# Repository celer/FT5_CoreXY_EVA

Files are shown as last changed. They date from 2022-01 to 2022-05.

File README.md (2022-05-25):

# Introduction 

This is a OpenSCAD based utility to generate a Folgertech FT5 to coreXY using the EVA 
carriage system used on the Ratrig printers, this is a work in progress. 

I'm using OpenSCAD for the design so it is fully parametric fully bed movement
can be simulated and pulley and belt sizes can be changed so belt paths can 
be simulated. This means that you can modify the openscad file based upon 
your available pulleys and belt and the correct design will be generated
for you. 

I've downloaded the STLs from the EVA project into this repo for ease of
use, see here: https://main.eva-3d.page

Nema17 model is from here: https://www.thingiverse.com/thing:67561
Endstop model is from here: https://www.thingiverse.com/thing:2405504/files

This is a work in progress and no STLs for printing have been created yet. 

## Goals

 * Gain the benefits of CoreXY, primarly improved print speed and print quality
 * Reuse as many peices as I can from my existing FT5
 * Share with the community so that others can extend the lives of their FT5s

## Top View
 * [Parallel A-H belt paths](https://drmrehorst.blogspot.com/2018/08/corexy-mechanism-layout-and-belt.html)

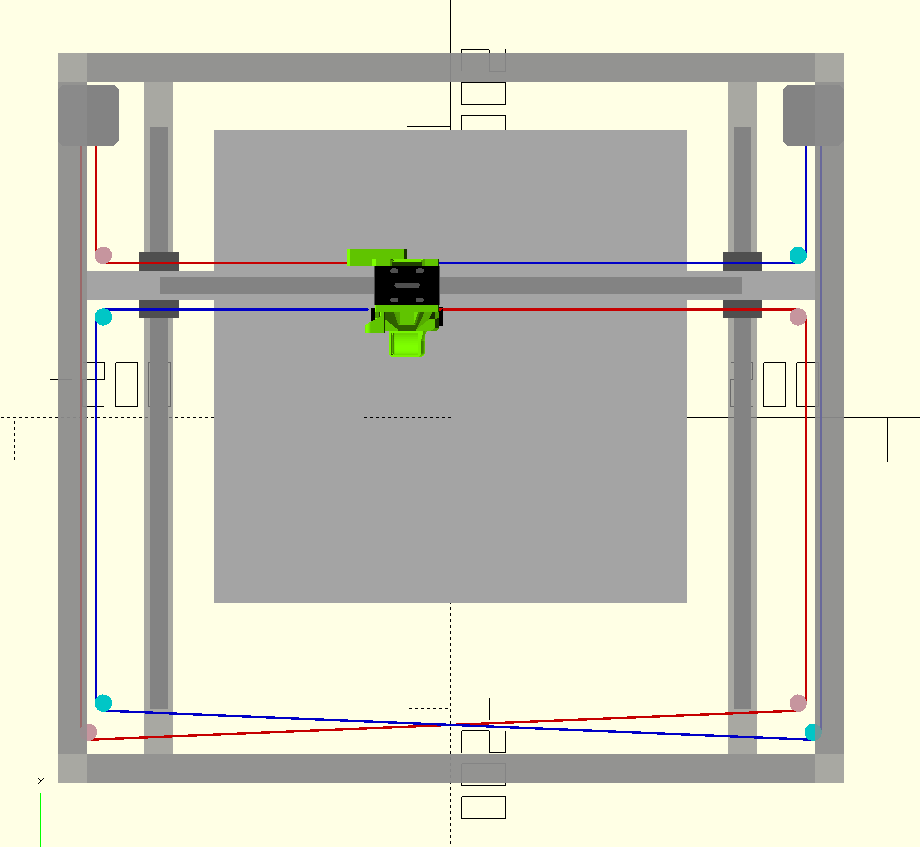
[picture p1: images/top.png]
Top


## Side views

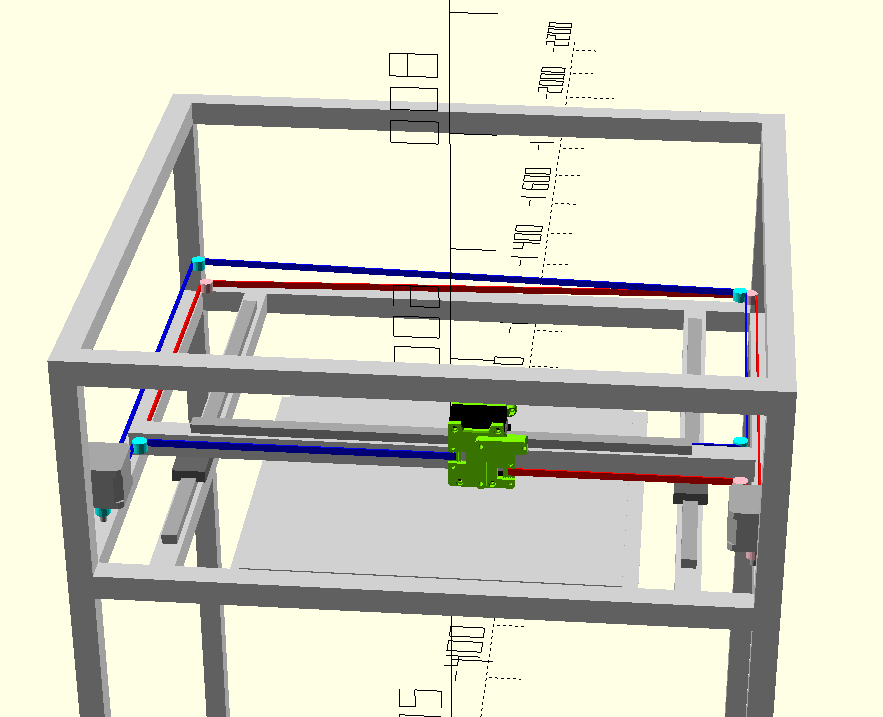
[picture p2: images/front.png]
Front

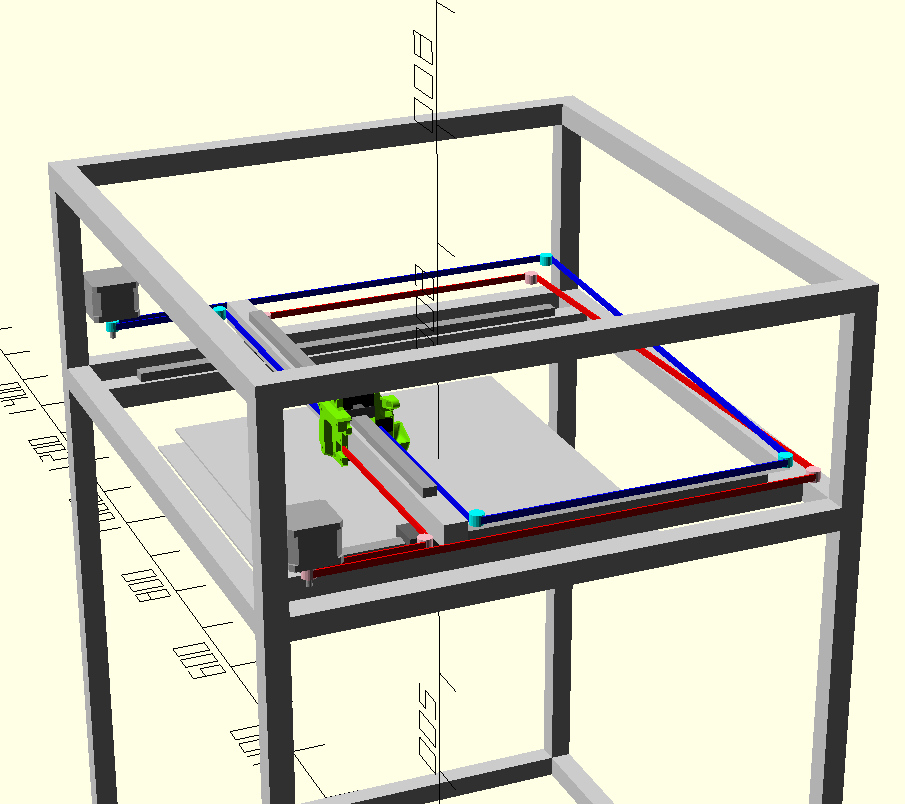
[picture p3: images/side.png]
Side

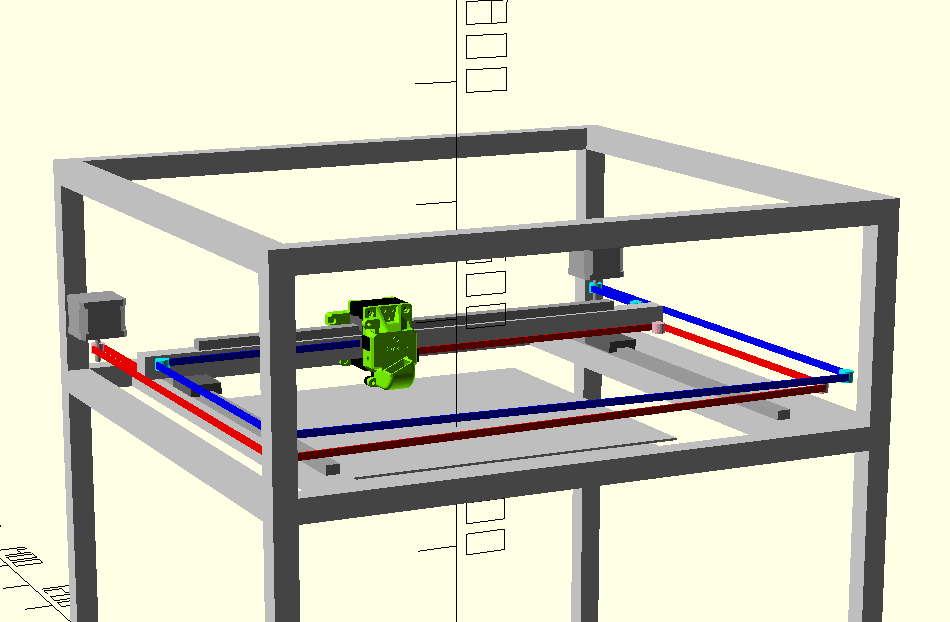
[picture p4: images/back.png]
Back


## Model view
Model

# Building

To build the stls you will need a linux environment with openscad installed, simply type 
'make' in the root of the directory and all the models will be generated. Or alternatively 
you can jump to the bottom of the .scad file and select specific models for printing. 

# Assembly

## Parts needed

See the bom.txt in this repo for a build of materials.

### Belts and Pulleys
The currently generated stls assume that you're using a Gates 6mm belt and pulleys, such 
a kit can be acquired from here: https://www.filastruder.com/products/gates-motion-set-for-railcore?_pos=5&_sid=bafef878a&_ss=r

I choose this belt kit because chinese / lesser quality belts stretch and may give poor results. 

This particular kit includes 2 smooth idler pulleys, 6 toothed idler pulleys, and 2 16 tooth motor pulleys. 

### Nuts and bolts

 * 20 M5x10MM bolts and t-slot nuts, which should be scavangable from your existing FT5 build
 * 2 M5x75MM bolts for the EVA carriage
 * An assortment of M3 
 * Shoulder bolts and shims for the pulleys - https://www.amazon.com/gp/product/B077GXK4P5/ref=ppx_yo_dt_b_asin_title_o08_s00?ie=UTF8&psc=1  https://www.filastruder.com/products/shims-for-shoulder-screws?_pos=1&_sid=fd8270e49&_ss=r

 ## What to print

  - You will need to print all the models in "stls/" folder, print these models with atleast 3 layer thickness, top bottom and side, and 40% infill.
  - You will need to choose and print an EVA extruder carriage, make sure to print the rear carriage tensors which allow for the teeth of the belts to face the rear of the printer
  - For the x axis you can either use your exisiting aluminum extrusion or go down the path of the carbon fiber square tube. I've included parts for the extrusion which are marked have the suffix *_al_2020.stl or *_cf_tube.stl which are for the carbon fiber square tube. See the section below on the carbon fiber square tube

## Assembly 

### Carbon Fiber Square Tube (optional)

Print out 2 copies of the xy_carriage_mount_cf_tube_upper_drill_jig.stl and use these two parts to align the holes to drill on the carbon fiber tube, the drill jig is setup so that it aligns the holes for the linear rail and then mounting brackets. I have not tested this drill jig, so you should use it with caution. You essentially drill the holes to mount the linear rail and end mounts, drilling through both sides of the square tube, find them smallest 1/4" socket which fits the M3 nuts required to attach the linear rail to the square tube and enlarge the holes on the bottom of the square tube so that you can fight the socket into the holds to tighten the linear rail to the carbon fiber rod. 
 
### Assemble the X rail 

1. Remove the old FT5 components 
2. You will need to insure that the XY carriage uppers and lowers have the 'F' near the front of the printer, the carriages are not symmetric front to back. 

### Assemble the Y rail

1. Remove the old FT5 components
2. Remove the top aluminum extrusion rail and assemble the motor mounts and rear pulley mounts with appropriate M5 and tslot nuts then with the top rectangle of the aluminum extrusion removed from the printer slide the motor and rear pulley mounts down into place. 

### Attach the belts

1. When attaching the belts you'll need to insure that the belts are level and parrallel to the main axis of the printer. 
2. Add the Y endstop

# Included Marlin settings

I have included my marlin Configuration.h and Configuration_adv.h

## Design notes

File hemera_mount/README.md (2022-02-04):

# Introduction

This is my quick and dirty corexy hemera mount which uses the same belt mounting locations as the EVA carriages. 

 * Compatible cable mounts to EVA mounting system
 * BL Touch mount
 * Cable mount

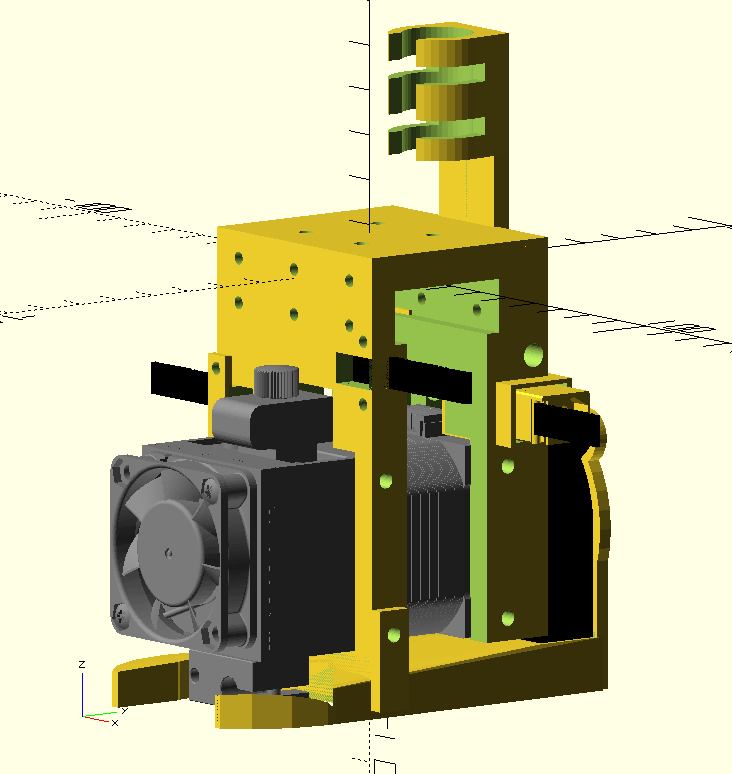
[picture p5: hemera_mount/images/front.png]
Front


# Notes
 
 * The "rear_eva_9mm_tension_slider.stl" is exported from the EVA repo (https://main.eva-3d.page/)
 * The Hemera model comes from https://www.thingiverse.com/thing:4016291/files by e3dsupport
 * The blower fan comes from https://www.thingiverse.com/thing:1576438/files by jimustanguitar

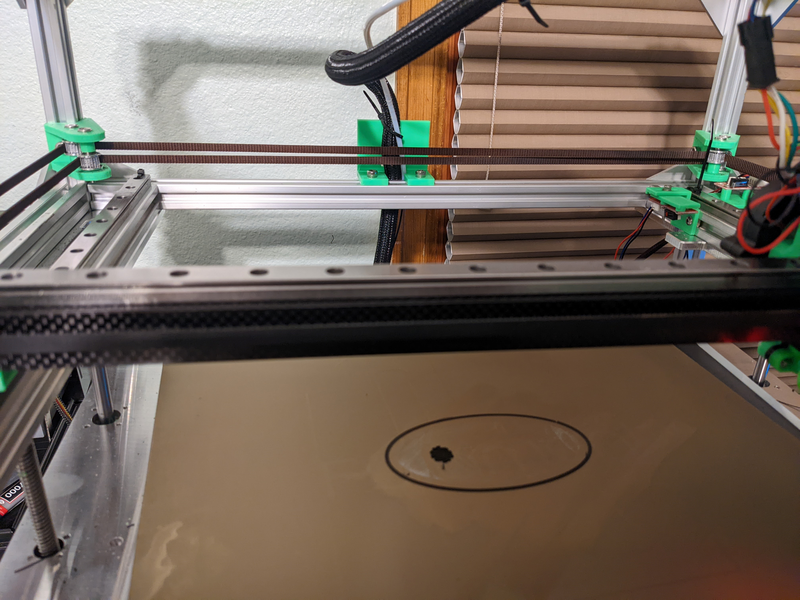
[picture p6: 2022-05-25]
photos/PXL_20220525_043905156.jpg.png

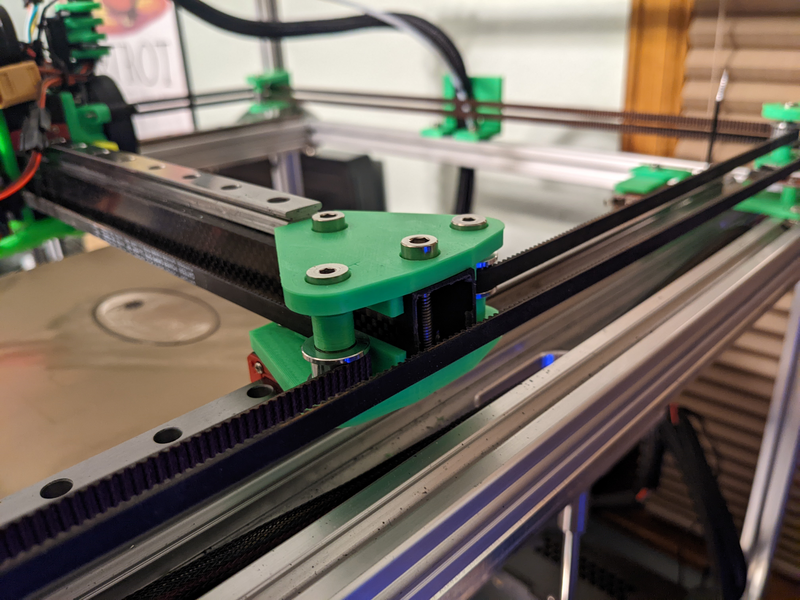
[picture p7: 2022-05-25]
photos/PXL_20220525_043838924.MP.jpg.png

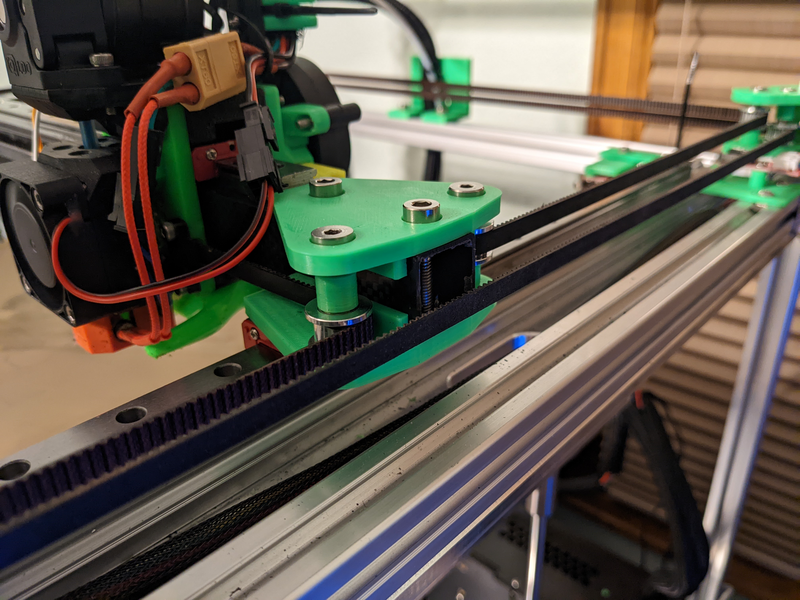
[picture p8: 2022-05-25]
photos/PXL_20220525_043833367.MP.jpg.png

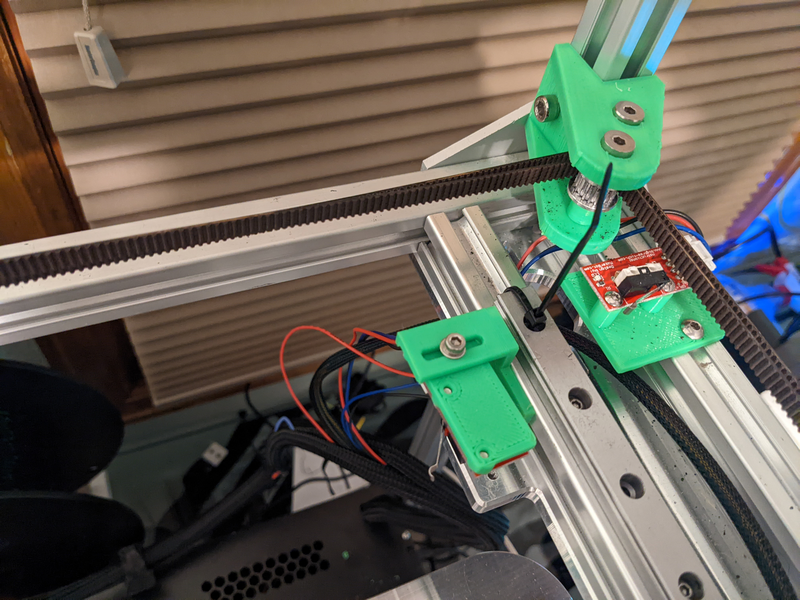
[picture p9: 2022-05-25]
photos/PXL_20220525_043824527.jpg.png

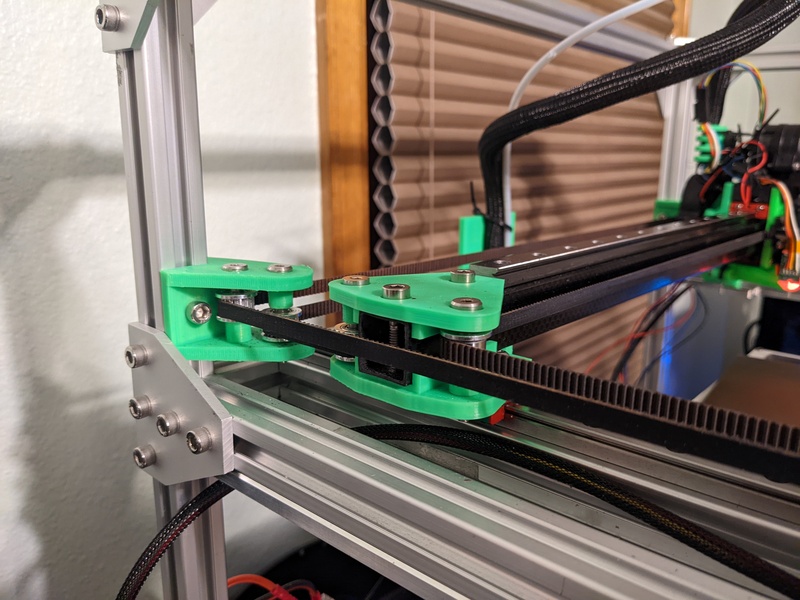
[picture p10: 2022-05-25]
photos/PXL_20220525_043754034.jpg.png

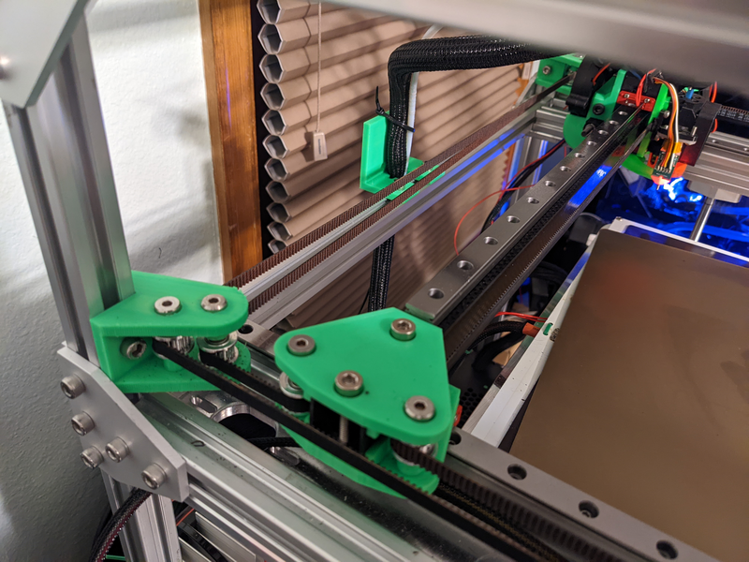
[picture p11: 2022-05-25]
photos/PXL_20220525_043800626.jpg.png

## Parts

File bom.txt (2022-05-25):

Raspberry PI 3b+

See this list for what is compatible with klipper

https://www.klipper3d.org/FAQ.html#can-i-run-klipper-on-something-other-than-a-raspberry-pi-3

From Ali Express (Carbon Fiber Square Tube for X Axis, optional):

1 X 20x20x500mm (the 500m is the only length they offer) 

https://www.aliexpress.com/item/32946654825.html?spm=a2g0o.order_list.0.0.dd8b1802j7lyNM

From BIQU: 

BIQU Phaetus Dragon Hotend (Make sure to select High Flow Option) (Optional)

https://www.biqu.equipment/products/bigtreetech-dargon-hotend-all-metal-copper-alloy-0-4mm-extruder-head-for-3d-printer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

F446 Controller Board (Make sure to select with 8 TMC2209 drivers), this is way overkill but it’s what is currently available. (Optional)

https://www.biqu.equipment/collections/control-board/products/bigtreetech-octopus-pro-v1-0-chip-f446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

From Printed Solid

Drive motor (There are two other alternatives to this the LGX Mini or the Sherpa Mini, I haven’t tested the options well enough to have a solid opinion on which one is the best - this is the one I’m currently testing, I think it’s better than the Sherpa mini, and will test an LGX mini soon):

https://www.printedsolid.com/products/bondtech-lgx-lite-large-gears-extruder?variant=39664965877845
 
or

https://www.printedsolid.com/products/ldo-orbiter-v2-dual-drive-direct-extruder

BL Touch (These are used to profile the bed level)
https://www.printedsolid.com/products/bltouch-automatic-bed-leveling-probe

From Filstruder:

Shims for pulleys

https://www.filastruder.com/products/shims-for-shoulder-screws?_pos=1&_sid=fd8270e49&_ss=r

Gates Belt Kit for RailCore Printer 300 ZL 

https://www.filastruder.com/products/gates-motion-set-for-railcore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

2 X Drive motors (42STH48-2504AC) - Optional, these enable higher speed printing, I haven’t fine tuned mine yet, but they should work better than the folgertech stepper motors

https://www.filastruder.com/products/ldo-stepper-motors-all-types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

From Amazon:

High performance bowden tube to keep the filament from spooling backwards

https://www.amazon.com/dp/B07PS3NH82?psc=1&ref=ppx_yo2ov_dt_b_product_details

These take the play out of the Z Axis (Optional)

https://www.amazon.com/gp/product/B08TLVL95C/ref=ppx_yo_dt_b_asin_title_o01_s00?ie=UTF8&psc=1

Anti-Vibration Feet, stop the rocking the printer does at high speed

https://www.amazon.com/dp/B0711Y6T56?psc=1&ref=ppx_yo2ov_dt_b_product_details

2 X Larger Z axis pulleys, these allow you to 2x the X axis resolution, you’ll also need a new belt, but I don’t know what size you’d need to measure after you test fit these: 

https://www.amazon.com/gp/product/B07K6BRL4K/ref=ppx_yo_dt_b_asin_title_o04_s00?ie=UTF8&psc=1

For the carbon fiber tube (Optional if you want to run carbon fiber x axis)

https://www.amazon.com/dp/B073TRJP6K?psc=1&ref=ppx_yo2ov_dt_b_product_details

1 set of M3 nuts (Optional if you want to run a carbon fiber x axis)
https://www.amazon.com/dp/B071NLDW56?psc=1&ref=ppx_yo2ov_dt_b_product_details

1 set of M3 washers (Optional if you want to run carbon fiber x axis)
https://www.amazon.com/dp/B075GVHLQ4?psc=1&ref=ppx_yo2ov_dt_b_product_details

You may need these for the hot end
https://www.amazon.com/dp/B08R9G2VDR?ref=ppx_yo2ov_dt_b_product_details&th=1

Shoulder Bolts, these are used on the corner pulleys and x axis
https://www.amazon.com/gp/product/B077GXK4P5/ref=ppx_yo_dt_b_asin_title_o08_s00?ie=UTF8&psc=1

HDMI Touchscreens & cables to hook up to the Raspberry PIs - You can choose any raspberry pi touch screen, the one I linked is the one I have, you’ll need cables as well. 
https://www.amazon.com/gp/product/B09LLC4H3Q/ref=ppx_yo_dt_b_search_asin_title?ie=UTF8&th=1

Set of fans 40x40x10 for the hot ends::
https://www.amazon.com/gp/product/B088BF6H8P/ref=ppx_yo_dt_b_asin_title_o00_s00?ie=UTF8&psc=1

Misc hardware:

8x M5x30 metric bolts & nuts 
4x M5x75 metric bolts & nuts

You’ll probably need extra wires, and some misc metric hardware.

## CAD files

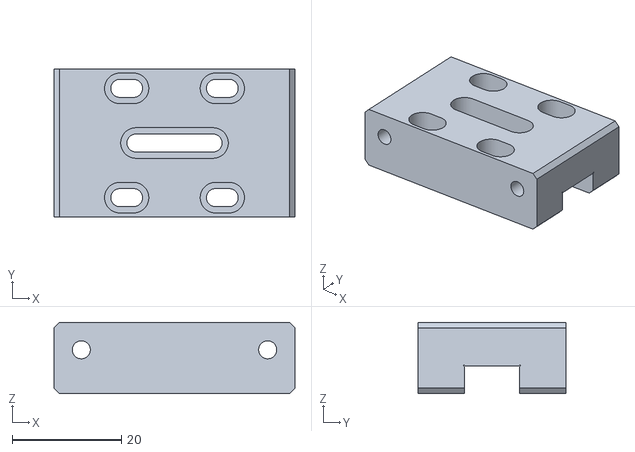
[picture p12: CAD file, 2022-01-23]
eva_hemera/top_mgn12.stl
44.1 x 27.0 x 13.0

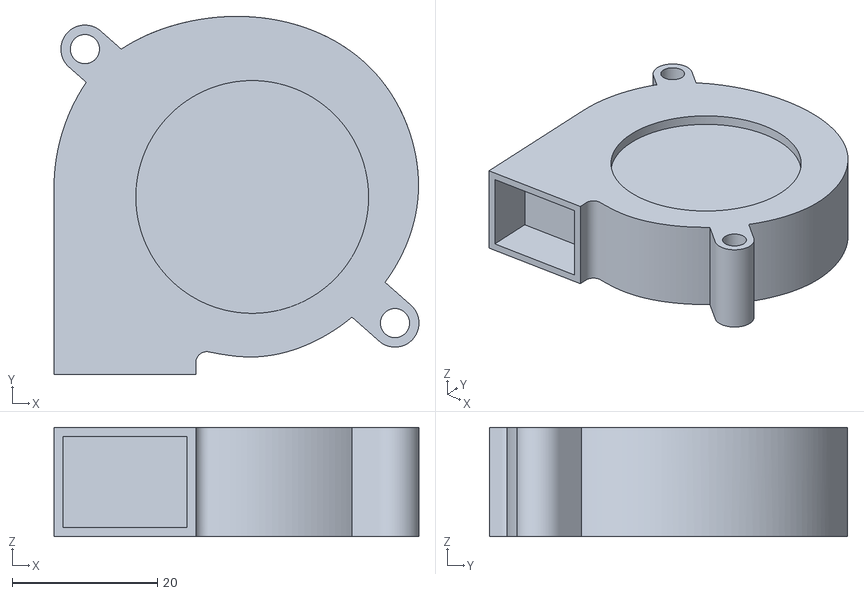
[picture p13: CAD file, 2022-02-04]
hemera_mount/models/5015_Blower_Fan.stl
50.2 x 49.2 x 15.0

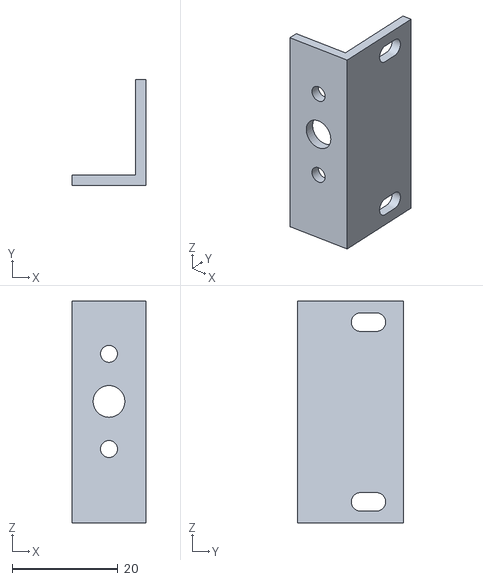
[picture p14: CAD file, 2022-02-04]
hemera_mount/stls/bl_touch_mount.stl
14.0 x 20.0 x 42.0

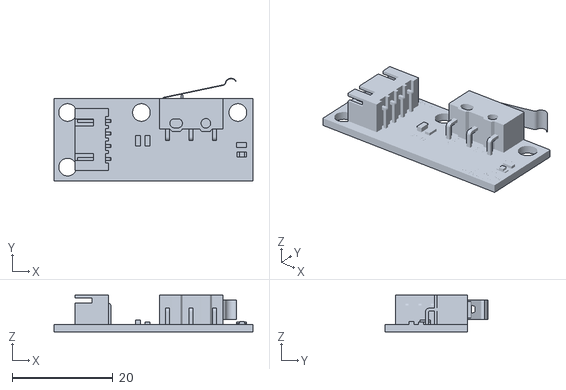
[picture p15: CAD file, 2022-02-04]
models/MakerBot_Endstop.stl
39.5 x 20.3 x 7.30

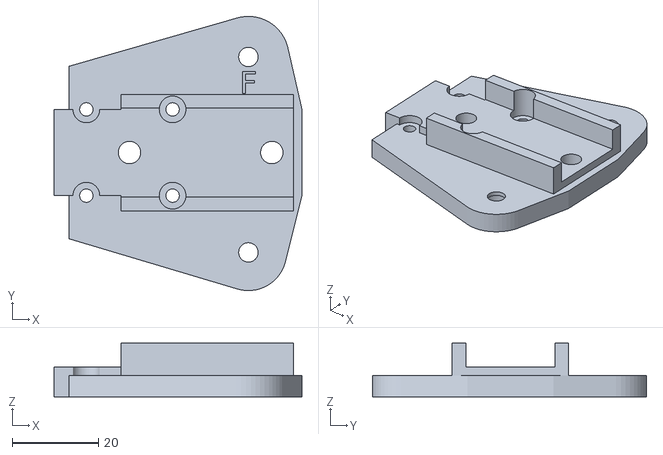
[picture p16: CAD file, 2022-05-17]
stls/left_xy_carriage_mount_lower_cf_tube.stl
57.5 x 63.6 x 12.5

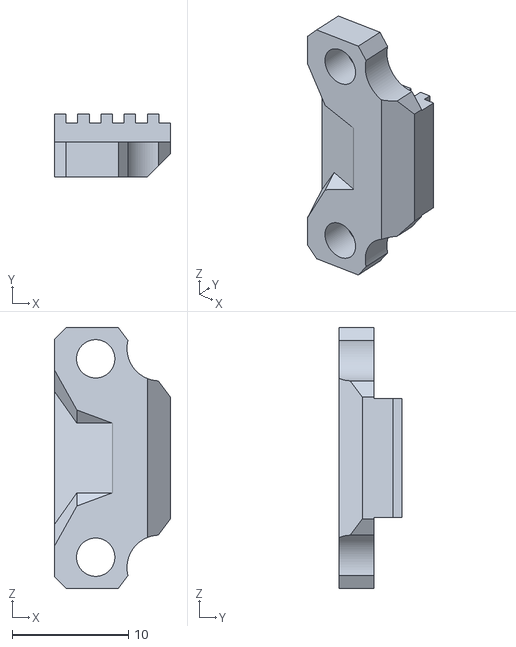
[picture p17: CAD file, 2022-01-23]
eva_hemera/face_belt_grabber.stl
10.0 x 5.40 x 22.5

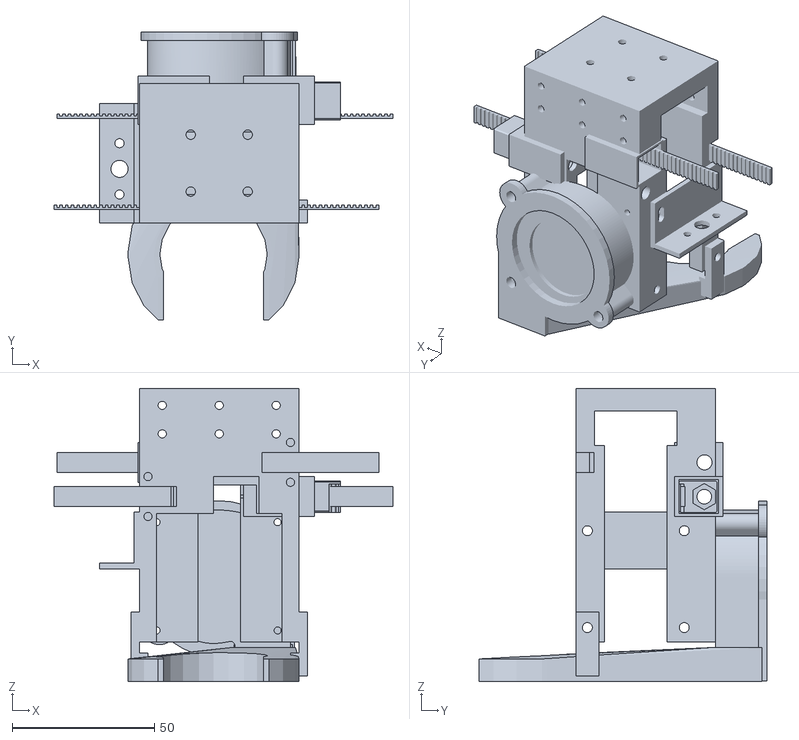
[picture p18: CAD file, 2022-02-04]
hemera_mount/stls/hemera_eva.stl
119.0 x 101.0 x 103.0

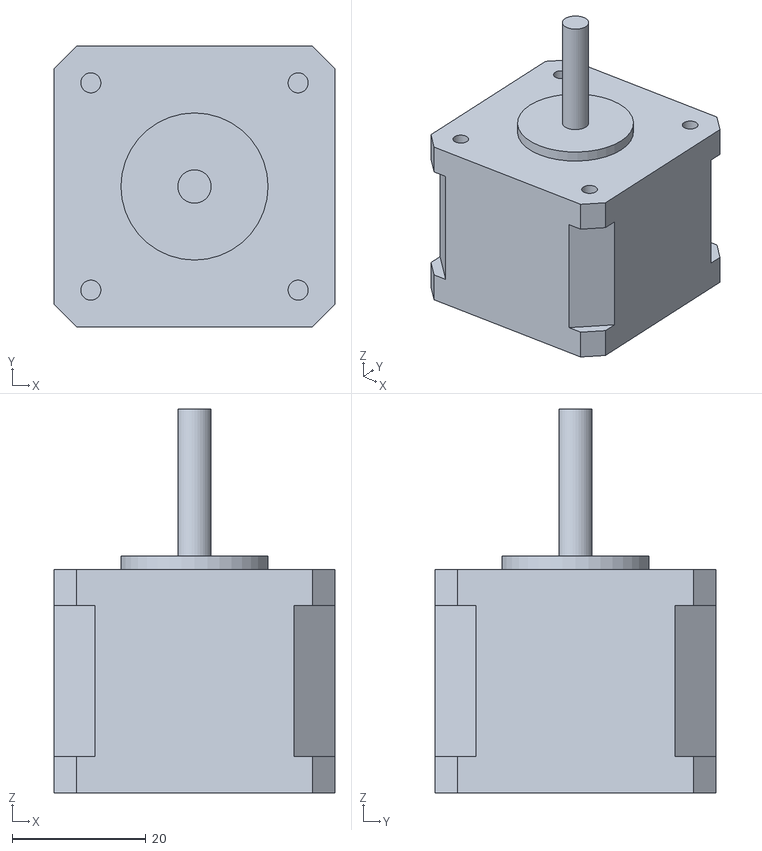
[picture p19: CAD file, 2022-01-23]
models/Motor_NEMA17.stl
42.0 x 42.0 x 57.4

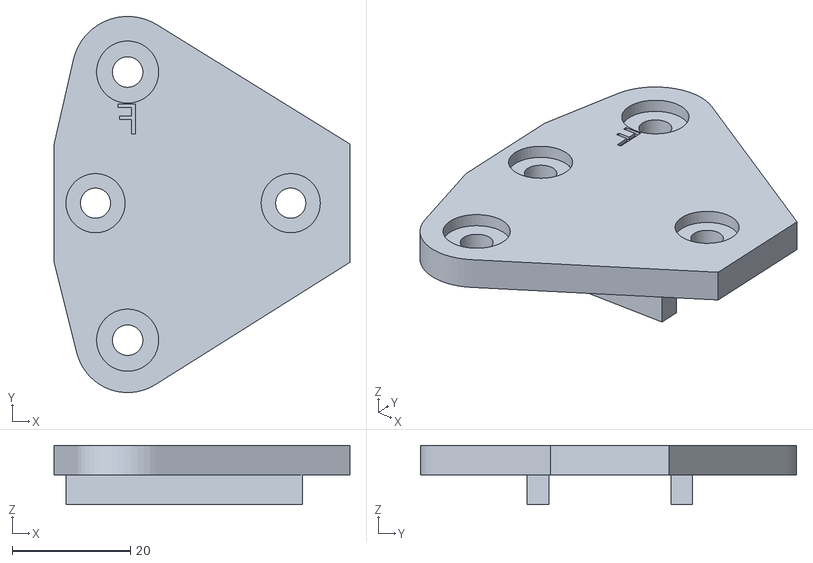
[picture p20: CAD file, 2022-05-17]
stls/right_xy_carriage_mount_upper_cf_tube.stl
50.0 x 63.6 x 10.0

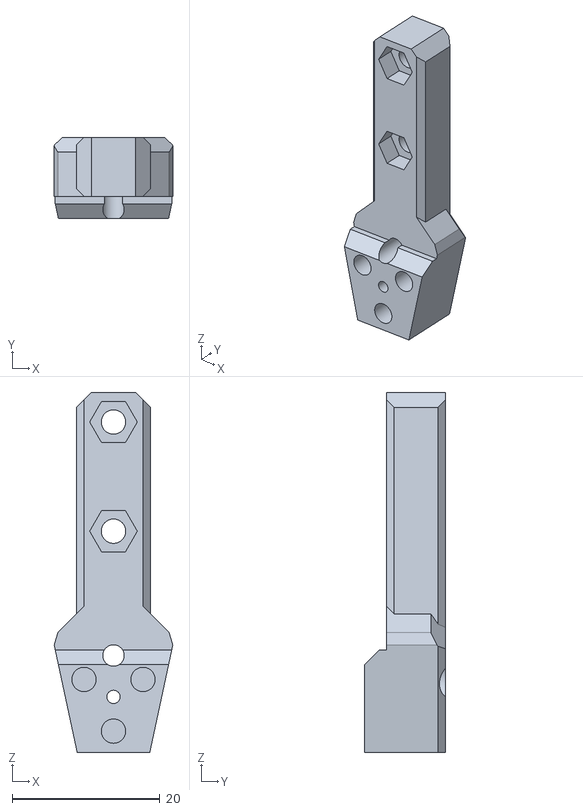
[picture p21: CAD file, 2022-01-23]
eva_hemera/unversal_cable_mount.stl
16.1 x 11.0 x 48.8

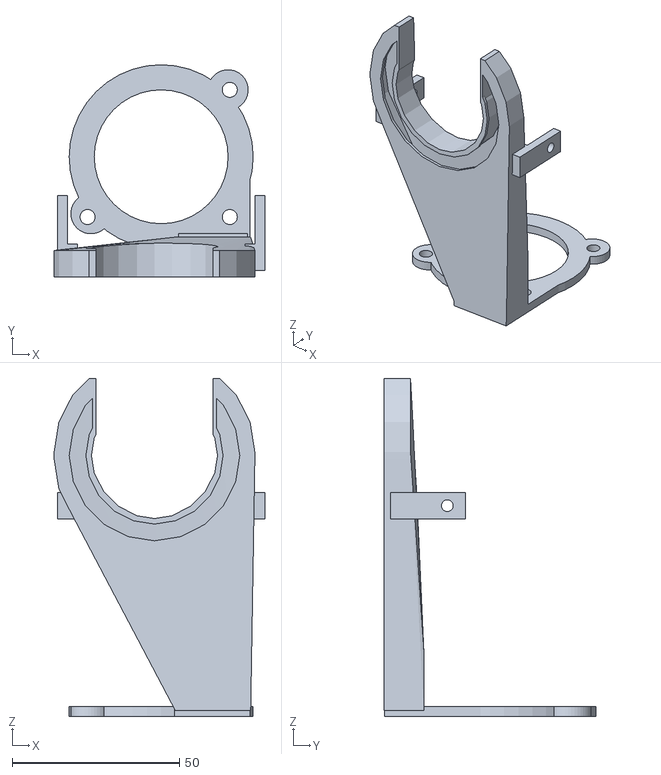
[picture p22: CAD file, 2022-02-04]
hemera_mount/stls/duct.stl
63.0 x 63.5 x 101.0

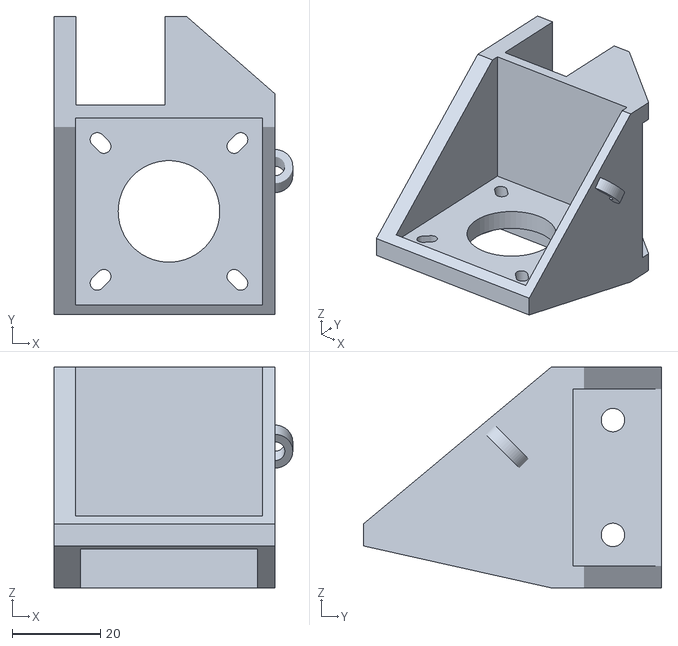
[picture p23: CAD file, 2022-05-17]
stls/right_motor_mount.stl
54.1 x 67.5 x 50.0

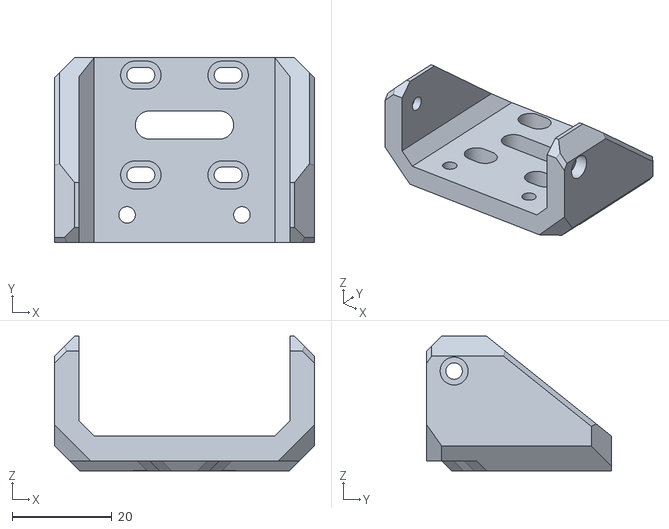
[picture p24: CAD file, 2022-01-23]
eva_hemera/top_lgx_mgn12_b.stl
52.1 x 37.0 x 27.0

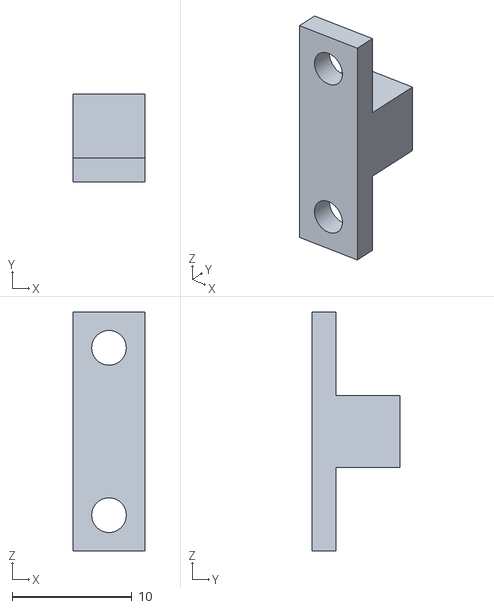
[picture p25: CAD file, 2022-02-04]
hemera_mount/stls/front_belt_mount.stl
6.00 x 7.32 x 20.0

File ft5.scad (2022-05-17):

// Introduction    //////////////////////////////////////////////
/////////////////////////////////////////////////////////////////
// 1. Measure and define your pulleys
//
// To get a CoreXY system working well the belts *MUST* be parallel
// to the axies, which means we need to accurately measure our belts
// and pulleys.
// 

// 1. Pulley definitions ///////////////////////////////////////////
////////////////////////////////////////////////////////////////////
// The pulley definitions define details about the pulleys which are critical to getting
// a precise corexy movement, the front belts MUST be parallel to their respective axis.

// The DWB = Diameter with belt - this the measurement of the diameter of the pulley
// with the belt on it. 

//// Motor pully definitions

///// Motor Pulley Height
MotorPulleyH = 16;   

//// Motor Pulley Diamater With Belt
MotorPulleyDWB = 11.04;

//// X Axis Pulleys
////////////////////////////////////////////////////////////////////
// X Axis Pulley details, I have accounted for the smooth pullyes seperately because
// they will have a different diameter than the toothed pulleys

// X Pulley Smooth Height
XPulleySmoothH = 10;
// X Pulley Smooth Diameter with Belt
XPulleySmoothDWB = 14.82;

// X Axis Pulley details, this can be toothed or smooth
// X Pulley Toothed Height
XPulleyToothedH = 10;
// X Pulley Toothed Diameter with Belt
XPulleyToothedDWB = 13.72;

// Rear left and right corner Pulley details
CornerPH = 10; // Height
CornerPDWN = 13.72; // Outside diameter with belt
CornerPulleyMountSpacer=1;

//////////////////// FT5 Dimensions //////////////////////////////////////////////
//
// I've measured these somewhat accurately but thit's worth double checking.
//
// This is the distance between the centers of the exterior 2020 extrusions, measured 
// at center
ExteriorWidth = 520;
ExteriorDepth = 482;

// The inteior space of the XY carriage area 
// measured center of extrusion to center of extrusion
InteriorWidth = ExteriorWidth-100;

InteriorDepth = ExteriorDepth;

// Center of XY Carriage height
XYCarriageHeight = 532;

// Total Length of the 2020 extrusion for the X axis
X2020Length = ExteriorWidth-20;

// FIXME this has an issue with hitting the Y blocks. 
// How far off the Y MGN12 block the X 2020 extrusion is
XCarriageMountHeight = 7;

// Overall height of the printer
Height = 720;

//This is how thick the belt is so the front pulleys can be placed correctly
BeltThickness = 1.50;

// The height of the belt, in theory changing this to a wider belt should just work
BeltHeight = 5.8;

MotorX = 42.3;
MotorY = 42.3;

// Total height of an MGN12 rail and block 
MGN12Height = 13;

//How much to offset each pulley so that doesn't interfer with the others
RearPulleyOffset = 10;


// Z Axis dimensions
ZAxisLinearRodOffsetsFromFront=[117,317];
ZAxisMotorOffset=215.5;
ZAxisSideOffset=60;

// Enclosure
EnclosureWidth=495;
EnclosureHeight=172;
EnclosureDepth=78+5;

///////////////////////////////////////////// EVA Platform ////////////////////////////////
/// The EVA Carriage platform is meant to allow easy swapping of carriages so this is used
// by the ratrig guys to make it easy to support multiple extruders. 
// see https://main.eva-3d.page/

// Belt Offsets as calculated from the center of X MGN12 block
EVAFrontBeltY = 15.5;

// Center of the belt offset as calculated from the center top of the MGN12 block
EVAFrontUpperBeltZ = -18;
EVAFrontLowerBeltZ = -30;

// Center of the belt offset as calculated from the center top of the MGN12 block
EVAFrontUpperBeltX = 17;
EVAFrontLowerBeltX = -26;

// Belt Offsets as calculated from the X block
EVABackBeltY = -16.5;

EVABackLowerBeltZ = -30;
EVABackUpperBeltZ = -18;

EVABackLowerBeltX = 20;
EVABackUpperBeltX = -27;

Extrusion2020Height = 20;
Extrusion2020Width = 20;

/*
EVABackLowerBelt() color("red") cube([20,1.6,6],center=true);
EVABackUpperBelt() color("blue") cube([20,1.6,6],center=true);

EVAHemeraCarriage();*/

///////////////////////////////////////// BED Details /////////////////////////////////////////

// The bed is 35mm forward of the Y center, AFAIK
BedCenterY = 35;

BedX = ExteriorWidth-220+25;
BedY = 325;

////////////////////////////////////////// XY Carriage center on the bed /////////////////////////
// Change this to simulate movement
X = 150;  //(-150 to 150)
Y = 150;  //(-150 to 150)


// Calculated location
YLocation = InteriorDepth/2 - BedCenterY+X;
XLocation = InteriorWidth/2 + Y;


// Calculated upper and lower belt heights
LowerBeltHeight = XYCarriageHeight + Extrusion2020Height/2 +
                MGN12Height + XCarriageMountHeight + Extrusion2020Height + MGN12Height + EVAFrontLowerBeltZ;

UpperBeltHeight = XYCarriageHeight + Extrusion2020Height/2 + 
                MGN12Height + XCarriageMountHeight + Extrusion2020Height + MGN12Height + EVAFrontUpperBeltZ;

//cube([520,20,20],center=true);
//translate([0,0,XYCarriageHeight-10]) cube([400,20,20],center=true);



module frame(){
     union() color("lightgrey") {
        for(x=[-ExteriorWidth/2,ExteriorWidth/2]){
            for(y=[-ExteriorDepth/2,ExteriorDepth/2]){
                  translate([x,y,Height/2]) cube([20,20,Height],center=true); 
            }
        }
                
   
        // XYCarriage
        translate([0,-ExteriorDepth/2,XYCarriageHeight]) cube([ExteriorWidth-20,20,20],center=true);
        translate([0,ExteriorDepth/2,XYCarriageHeight]) cube([ExteriorWidth-20,20,20],center=true);
        
        translate([-ExteriorWidth/2,0,XYCarriageHeight]) cube([20,ExteriorDepth-20,20],center=true);
        translate([ExteriorWidth/2,0,XYCarriageHeight]) cube([20,ExteriorDepth-20,20],center=true);
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

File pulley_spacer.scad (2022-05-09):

$fn=40;


translate([0,12,0]) difference(){
    cylinder(r=10/2,h=10);
    cylinder(r=5.15/2,h=12);
}

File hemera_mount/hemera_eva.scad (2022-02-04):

/*
    Sorry this is quite a bit of a mess, and is carried over from a prior design
*/

// Belt Offsets as calculated from the center of X MGN12 block
EVAFrontBeltY = 15.5;

// Center of the belt offset as calculated from the center top of the MGN12 block
EVAFrontUpperBeltZ = -18;
EVAFrontLowerBeltZ = -30;

// Center of the belt offset as calculated from the center top of the MGN12 block
EVAFrontUpperBeltX = 17;
EVAFrontLowerBeltX = -26;

// Belt Offsets as calculated from the X block
EVABackBeltY = -16.5;

EVABackLowerBeltZ = -30;
EVABackUpperBeltZ = -18;

EVABackLowerBeltX = 20;
EVABackUpperBeltX = -27;

module stepper_mount_holes(){
	translate([0,-38,-17]){
		for(x=[0,34]){
			for (y=[0,34]){
				translate([0,y,x]) rotate([0,90,0]) cylinder(r=3.5/2,h=100,center=true);
			}
		}
	}
}


module mount() {
    difference(){
        union(){
            translate([0,0,-38]) rotate([90,0,0]) difference(){
                
                //Main block
                union(){
                    translate([0,1.5,-3.5]) cube([56,86+3,42+7],center=true);
                
                    
                    translate([0,1.5,-42/2]) difference(){
                        cube([56,86,7],center=true);
                    }
                    

                }
                
                fan_holes(2.5);
                
                // Screw holes for mounts
                for(x=[-20:20:20]){
                    for(y=[-5,5]){
                        translate([x,35+y,25]) cylinder(r=2.9/2,h=90,center=true);
                        translate([x,35+y,-25]) cylinder(r=2.9/2,h=90,center=true);
                    }
                }
                
                // Cut out for the rail and slider
                translate([0,32,0]) cube([100,12,29],center=true);
                translate([0,-6,0]) cube([100,88,22],center=true);


                // Cut out for the stepper motor
                translate([0,-23,0]) cube([44,50,43],center=true);
                
                // Cut out for rear stepper cables
                translate([0,-20,-12]) cube([26,64,19],center=true);
                
                // Cut out for rear stepper cables
                translate([0,-20,-22]) cube([15,64,19],center=true);
                
                // Cut out for front handle
                translate([6,-20,20]) cube([16,70,50],center=true);
                
                
                // Mounts for the stepper motor
                stepper_mount_holes();
                

                
                //Slide rail mounts
                for(x=[-10,10]){
                    for(z=[-10,10]){
                        translate([x,40,z]) rotate([90,0,0]) cylinder(r=3.3/2,h=20,center=true);
                    }
                }     
            }
           
 
           
            translate([EVABackUpperBeltX,-EVABackBeltY,EVABackUpperBeltZ]) translate([11,5.6,0]){
                cube([25,17,14],center=true); 
            }
            translate([EVABackLowerBeltX,-EVABackBeltY,EVABackLowerBeltZ]) translate([1,5.6,0]) {
                cube([25,17,14],center=true);
            }
        }
        
        translate([EVABackUpperBeltX,-EVABackBeltY,EVABackUpperBeltZ]) translate([10,5.6,0]){
            cube([25,14,12],center=true); 
            translate([0,2,0]) rotate([0,90,0]) cylinder(r=5.3/2,h=200,center=true);
        }
        translate([EVABackLowerBeltX,-EVABackBeltY,EVABackLowerBeltZ]) translate([2,5.6,0]) {
            cube([25,14,12],center=true);
            translate([0,2,0]) rotate([0,90,0]) cylinder(r=5.3/2,h=200,center=true);
        }
        for(y=[0:-0.6:-10]){
            translate([EVAFrontLowerBeltX-2,-EVAFrontBeltY+y,EVAFrontLowerBeltZ]) gt2_belt(); 
            translate([EVAFrontUpperBeltX-2,-EVAFrontBeltY+y,EVAFrontUpperBeltZ]) gt2_belt();
        } 
      
        translate([EVAFrontLowerBeltX+1,-EVAFrontBeltY,EVAFrontLowerBeltZ]) rotate([90,0,0]) {
            for(z=[-7,7]){
                translate([0,z,5]) cylinder(r=2.9/2,h=10,center=true);
            }
        }
        translate([EVAFrontUpperBeltX+8,-EVAFrontBeltY,EVAFrontUpperBeltZ]) rotate([90,0,0]) {
            
            for(z=[-7,7]){
                translate([0,z,5]) cylinder(r=2.9/2,h=10,center=true);
            }
        }
        
        rotate([90,0,0]) translate([0,-38,0]) fan();
    }
    

   
}

//front_belt_mount();
cable_mount();
//mount();

module cable_mount(){
    translate([0,29,9]){
        difference(){
            union(){
                hull(){
                    translate([0,-10,15]) cylinder(r=22/2,h=27);
                    translate([0,0,28.5]) cube([20,4,27],center=true);
                }
                translate([0,0,11]) cube([20,4,62],center=true);
            }
            //translate([0,-13,25]) cylinder(r=16/2,h=50,center=true);
            translate([0,-10,25]) cylinder(r=16/2,h=50,center=true);

            for(z=[0:12:25]){
                translate([0,-17,22+z]) cube([24,24,4],center=true);
            }
            
            translate([0,-17,29]) cube([10,10,40],center=true);

            


        translate([0,0,-12]){
        for(z=[5,-5]){
            translate([0,0,z]) rotate([90,0,0]) cylinder(r=3.3/2,h=560,center=true);
        }   
    }
    }
    }
}

front_belt_mount();

module front_belt_mount(){
        
     
        difference(){
            union(){
                translate([EVAFrontLowerBeltX-2 ,-EVAFrontBeltY-3,EVAFrontLowerBeltZ]) translate([0,-3.4,-3])  cube([6,6,6]);
                translate([EVAFrontLowerBeltX-2 ,-EVAFrontBeltY-3,EVAFrontLowerBeltZ]) translate([0,-4.9,-10])  cube([6,2,20]);
            }
            for(z=[-7,7]){
                translate([EVAFrontLowerBeltX+1,-EVAFrontBeltY-3,EVAFrontLowerBeltZ+z]) rotate([90,0,0]) cylinder(r=2.9/2,h=1000,center=true);
            }
            translate([EVAFrontLowerBeltX-2,-EVAFrontBeltY+0.2,EVAFrontLowerBeltZ]) gt2_belt(); 
       }

        
        
}

module gt2_belt(len=12){
    translate([0,-1.55/2,-3.5]){
        cube([len,1.55-0.75,7]);
        for(r=[0:2:len]){
            translate([r,0,0]) cube([1.0,1.55,7]);
        }   
    }
}

module bl_touch_mount(){
	difference(){
		translate([-30,-17.8+0.4,-42/2]){
			cube([2,20,42]);
			translate([-12,0,0]) cube([12,2,42]);
		}
		bl_touch();
		for (z=[-1.5:0.25:1.5]){
			translate([0,z,0]) stepper_mount_holes();
		}
	}
}

module bl_touch(){
	translate([-35,-17.8+0.4,2]){ 
		rotate([90,0,0]) cylinder(r=8/2,36.3);
		rotate([90,0,0]) translate([0,0,-10]) cylinder(r=6/2,h=10);
		for(z=[9,-9]){
			translate([0,0,z]) rotate([90,0,0])translate([0,0,-10]) cylinder(r=3.2/2,h=10);
		}
	}
	
}

module hemera(){
	   translate([-24,-62.6,-20.5]) import("models/HEMERA-MODEL-1.1.STL");

}


module airflow_exitfan(d=0){
     translate([5.25,-56,-40.25-3]) cube([20.5,10+d,15.5]);
}



nozzle_x=-2;
nozzle_y=-53;
nozzle_z=32;

module airflow_exhaust(d=0,r=58,h=6){
    // translate([-20,-71+d,25]) rotate([0,-30,0]) cube([8,5,20]);
	translate([nozzle_x,nozzle_y,nozzle_z]) rotate([90,0,0]) translate([0,0,d]){ 
			cylinder(r=r/2,h=h,center=true,$fn=20);
	}
}



module airflow(){
        difference(){
            hull(){
                airflow_exitfan(); 
                airflow_exhaust();
            }
			
			airflow_exhaust(r=40,h=100);
			translate([nozzle_x,nozzle_y,nozzle_z+25]) cube([37,20,60],center=true);
					
        }   
}

module airflow_fins(){
	intersection(){
	intersection(){
		intersection(){
			union(){
				 for(x=[-24:6:26]){
					translate([x-2,-55,10]) cube([1.2,20,60],center=true);
				}
			}
			
			translate([0,0,10]) airflow();
			
		}
		translate([0,0,0]) airflow();
	}
	}
}


module duct(){
	
	//airflow_fins();
	
    difference(){
		union(){
		   
			translate([0,-21,-46])  difference(){
				union(){
					translate([4,-35.8,0]) cube([22.5,37,3]);
					cylinder(r=55/2,h=3);
					
					translate([20,20,0]) cylinder(r=12/2,h=3);
					translate([-21,-17,0]) cylinder(r=12/2,h=3);
					
					translate([0,-30,63]) difference(){
						cube([62,8,8],center=true);
						cube([50,8,8],center=true);

					}
					translate([0,-22,63]) difference(){
						cube([62,21,8],center=true);
						cube([56,21,8],center=true);
					}
				}
				cylinder(r=40/2,h=3);
				
			}
			
			
			difference(){
				minkowski(){
					airflow();
					cube([2,2,2],center=true);
				}
			}
			
		}
		fan_holes(4.5);
		// Mounts for the stepper motor
		stepper_mount_holes();
		
		airflow();	
		airflow_exitfan(2);
		
		
		// airflow_exhaust(5,r=52);
		difference(){
			airflow_exhaust(5,r=51);
			airflow_exhaust(5,r=41);
			translate([nozzle_x,nozzle_y,nozzle_z+25]) cube([37,20,60],center=true);
		}
    }
}

module fan_holes(r=3.1){
    for(x=[-22,20.5]){
        for(y=[-19,19]){
            translate([x,y-20,-50]) cylinder(r=r/2,h=50);
        }
    }
}


module duct_mount(){
     translate([4,-56,-40.25]) cube([24,14,18]);
     translate([2,-49,-d/2+5]) cube([w,14,6],center=true);
}
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

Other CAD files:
stls/left_xy_carriage_mount_lower_al_2020.stl
eva_hemera/tension_slider_9mm_belt_M5.stl
hemera_mount/stls/mount.stl
stls/rear_left_pulley_mount.stl
eva_hemera/Duct v21 Angled 132deg.stl
eva_hemera/back_corexy.stl
eva_hemera/bottom_mgn12_hemera.stl
eva_hemera/bottom_mgn12_short_duct.stl
eva_hemera/cable_holder.stl
eva_hemera/hemera_face.stl
eva_hemera/hemera_probe_adapter.stl
eva_hemera/top_lgx_mgn12_a.stl
eva_hemera/universal_face.stl
hemera_mount/stls/cable_mount.stl
hemera_mount/stls/rear_eva_9mm_tension_slider.stl
stls/left_motor_mount.stl
stls/left_xy_carriage_mount_upper_al_2020.stl
stls/left_xy_carriage_mount_upper_cf_tube.stl
stls/rear_right_pulley_mount.stl
stls/right_xy_carriage_mount_upper_al_2020.stl
stls/x_endstop_rail_mount.stl
stls/x_endstop_sensor_mount.stl
stls/xy_carriage_mount_cf_tube_upper_drill_jig.stl
stls/y_endstop_mount.stl

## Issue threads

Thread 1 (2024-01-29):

Not particularly a issue but possible update/upgrade

limback75, 2024-01-29:
The snakeoilxy has what they call 4pr which they combine the ft5 and your corexy into a extended corexy kinematic.  Increasing the speed even more for the ft5.

celer, 2024-01-29:
That is really cool to know! I am pondering building another printer and it's good to know about another option.

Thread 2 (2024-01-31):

STL files are missing the Right Lower XY Carriage Mount

TheeDynamikOne, 2024-01-31:
Hello Celer,

I'm working on this conversion, using the carbon tube. I noticed in the STL files the Right XY carriage mount lower cf & al files are missing. It looks like all the other STL files are present.

I attempted to pull the carriage mount file from OpenSCAD but I'm used to GUI based CAD programs and I'm failing miserably with OpenSCAD on Windows.

Thank you for your time and contribution to the good ol' Folder Tech community. I've had my FT-5 since 2017 and I've invested too much time with upgrades but its always been fun. I have a Duet board, 0.9° steppers, 500w power supply, etc. I really enjoy these printers and they print really well when dialed in.

TheeDynamikOne, 2024-02-20:
Do you think I need a Linux environment to utilize these files with OpenSCAD properly?

When I try to use the make the file, I'm using the command prompt but I'm having issues with windows finding the proper directory to execute the make command.

When I try to open the FT-5 model in OpenSCAD I can open the model and manipulate the Customizer successfully, but I can't get OpenScad to export individual parts. I can render the entire printer but it renders it mainly as one piece so I can't get the individual parts out of it.

I have very little coding experience so I could be missing something obvious. I'm trying to work with ChatGPT to trouble shoot the errors I'm receiving in OpenScad but I keep going in circles.

celer, 2024-02-20:
Sorry I forgot to add those. It's a bit convoluted to get it to generate the parts required.

The missing parts should be there now.

Closed 2024-02-20.

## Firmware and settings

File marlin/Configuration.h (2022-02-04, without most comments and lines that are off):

#pragma once
#define CONFIGURATION_H_VERSION 02000903
#define STRING_CONFIG_H_AUTHOR "(celer, FT5 CoreXY)" // Who made the changes.
  #define MOTHERBOARD BOARD_BTT_SKR_V1_4_TURBO
#define SERIAL_PORT -1
#define BAUDRATE 250000
#define SERIAL_PORT_2 0
#define BAUDRATE_2 250000  // Enable to override BAUDRATE
#define CUSTOM_MACHINE_NAME "FT5"
#define MACHINE_UUID "FT5000000-0000-0000-0000-000000000032"
#define LINEAR_AXES 3
#if LINEAR_AXES >= 4
  #define AXIS4_NAME 'A' // :['A', 'B', 'C', 'U', 'V', 'W']
#endif
#if LINEAR_AXES >= 5
  #define AXIS5_NAME 'B' // :['A', 'B', 'C', 'U', 'V', 'W']
#endif
#if LINEAR_AXES >= 6
  #define AXIS6_NAME 'C' // :['A', 'B', 'C', 'U', 'V', 'W']
#endif
#define EXTRUDERS 1
#define DEFAULT_NOMINAL_FILAMENT_DIA 1.75
#define TEMP_SENSOR_0 5
#define TEMP_SENSOR_1 0
#define TEMP_SENSOR_2 0
#define TEMP_SENSOR_3 0
#define TEMP_SENSOR_4 0
#define TEMP_SENSOR_5 0
#define TEMP_SENSOR_6 0
#define TEMP_SENSOR_7 0
#define TEMP_SENSOR_BED 75
#define TEMP_SENSOR_PROBE 0
#define TEMP_SENSOR_CHAMBER 0
#define TEMP_SENSOR_COOLER 0
#define TEMP_SENSOR_BOARD 0
#define TEMP_SENSOR_REDUNDANT 0
#define DUMMY_THERMISTOR_998_VALUE  25
#define DUMMY_THERMISTOR_999_VALUE 100
#define TEMP_RESIDENCY_TIME         10  // (seconds) Time to wait for hotend to "settle" in M109
#define TEMP_WINDOW                  1  // (°C) Temperature proximity for the "temperature reached" timer
#define TEMP_HYSTERESIS              3  // (°C) Temperature proximity considered "close enough" to the target
#define TEMP_BED_RESIDENCY_TIME     10  // (seconds) Time to wait for bed to "settle" in M190
#define TEMP_BED_WINDOW              1  // (°C) Temperature proximity for the "temperature reached" timer
#define TEMP_BED_HYSTERESIS          3  // (°C) Temperature proximity considered "close enough" to the target
#define TEMP_CHAMBER_RESIDENCY_TIME 10  // (seconds) Time to wait for chamber to "settle" in M191
#define TEMP_CHAMBER_WINDOW          1  // (°C) Temperature proximity for the "temperature reached" timer
#define TEMP_CHAMBER_HYSTERESIS      3  // (°C) Temperature proximity considered "close enough" to the target
#if TEMP_SENSOR_REDUNDANT
  #define TEMP_SENSOR_REDUNDANT_SOURCE    E1  // The sensor that will provide the redundant reading.
  #define TEMP_SENSOR_REDUNDANT_TARGET    E0  // The sensor that we are providing a redundant reading for.
  #define TEMP_SENSOR_REDUNDANT_MAX_DIFF  10  // (°C) Temperature difference that will trigger a print abort.
#endif
#define HEATER_0_MINTEMP   5
#define HEATER_1_MINTEMP   5
#define HEATER_2_MINTEMP   5
#define HEATER_3_MINTEMP   5
#define HEATER_4_MINTEMP   5
#define HEATER_5_MINTEMP   5
#define HEATER_6_MINTEMP   5
#define HEATER_7_MINTEMP   5
#define BED_MINTEMP        5
#define CHAMBER_MINTEMP    5
#define HEATER_0_MAXTEMP 275
#define HEATER_1_MAXTEMP 275
#define HEATER_2_MAXTEMP 275
#define HEATER_3_MAXTEMP 275
#define HEATER_4_MAXTEMP 275
#define HEATER_5_MAXTEMP 275
#define HEATER_6_MAXTEMP 275
#define HEATER_7_MAXTEMP 275
#define BED_MAXTEMP      150
#define CHAMBER_MAXTEMP  60
#define HOTEND_OVERSHOOT 15   // (°C) Forbid temperatures over MAXTEMP - OVERSHOOT
#define BED_OVERSHOOT    10   // (°C) Forbid temperatures over MAXTEMP - OVERSHOOT
#define COOLER_OVERSHOOT  2   // (°C) Forbid temperatures closer than OVERSHOOT
#define PIDTEMP
#define BANG_MAX 255     // Limits current to nozzle while in bang-bang mode; 255=full current
#define PID_MAX BANG_MAX // Limits current to nozzle while PID is active (see PID_FUNCTIONAL_RANGE below); 255=full current
#define PID_K1 0.95      // Smoothing factor within any PID loop
    #define DEFAULT_Kp  16.23
    #define DEFAULT_Ki   1.28
    #define DEFAULT_Kd  51.59
#define MAX_BED_POWER 255 // limits duty cycle to bed; 255=full current
#define MAX_CHAMBER_POWER 255 // limits duty cycle to chamber heater; 255=full current
  #define PID_FUNCTIONAL_RANGE 10 // If the temperature difference between the target temperature and the actual temperature
#define PREVENT_COLD_EXTRUSION
#define EXTRUDE_MINTEMP 170
#define PREVENT_LENGTHY_EXTRUDE
#define EXTRUDE_MAXLENGTH 200
#define THERMAL_PROTECTION_HOTENDS // Enable thermal protection for all extruders
#define THERMAL_PROTECTION_BED     // Enable thermal protection for the heated bed
#define THERMAL_PROTECTION_CHAMBER // Enable thermal protection for the heated chamber
#define THERMAL_PROTECTION_COOLER  // Enable thermal protection for the laser cooling
#define COREYX
#define USE_XMIN_PLUG
#define USE_YMIN_PLUG
#define USE_ZMIN_PLUG
#define ENDSTOPPULLUPS
#define X_MIN_ENDSTOP_INVERTING true // Set to true to invert the logic of the endstop.
#define Y_MIN_ENDSTOP_INVERTING true // Set to true to invert the logic of the endstop.
#define Z_MIN_ENDSTOP_INVERTING false // Set to true to invert the logic of the endstop.
#define I_MIN_ENDSTOP_INVERTING false // Set to true to invert the logic of the endstop.
#define J_MIN_ENDSTOP_INVERTING false // Set to true to invert the logic of the endstop.
#define K_MIN_ENDSTOP_INVERTING false // Set to true to invert the logic of the endstop.
#define X_MAX_ENDSTOP_INVERTING false // Set to true to invert the logic of the endstop.
#define Y_MAX_ENDSTOP_INVERTING false // Set to true to invert the logic of the endstop.
#define Z_MAX_ENDSTOP_INVERTING false // Set to true to invert the logic of the endstop.
#define I_MAX_ENDSTOP_INVERTING false // Set to true to invert the logic of the endstop.
#define J_MAX_ENDSTOP_INVERTING false // Set to true to invert the logic of the endstop.
#define K_MAX_ENDSTOP_INVERTING false // Set to true to invert the logic of the endstop.
#define Z_MIN_PROBE_ENDSTOP_INVERTING false // Set to true to invert the logic of the probe.
#define X_DRIVER_TYPE  TMC2209
#define Y_DRIVER_TYPE  TMC2209
#define Z_DRIVER_TYPE  TMC2209
#define E0_DRIVER_TYPE TMC2209
#define DEFAULT_AXIS_STEPS_PER_UNIT   { 100, 100, 800, 409 }
#define DEFAULT_MAX_FEEDRATE          { 300, 300, 5, 25 }
#define DEFAULT_MAX_ACCELERATION      { 3000, 3000, 100, 10000 }
#define DEFAULT_ACCELERATION          3000    // X, Y, Z and E acceleration for printing moves
#define DEFAULT_RETRACT_ACCELERATION  3000    // E acceleration for retracts
#define DEFAULT_TRAVEL_ACCELERATION   3000    // X, Y, Z acceleration for travel (non printing) moves
#define DEFAULT_EJERK    5.0  // May be used by Linear Advance
  #define JUNCTION_DEVIATION_MM 0.013 // (mm) Distance from real junction edge
  #define JD_HANDLE_SMALL_SEGMENTS    // Use curvature estimation instead of just the junction angle
#define USE_PROBE_FOR_Z_HOMING
#define BLTOUCH
#define NOZZLE_TO_PROBE_OFFSET { 30, 40, 0 }
#define PROBING_MARGIN 10
#define XY_PROBE_FEEDRATE (133*60)
#define Z_PROBE_FEEDRATE_FAST (4*60)
#define Z_PROBE_FEEDRATE_SLOW (Z_PROBE_FEEDRATE_FAST / 2)
#define Z_CLEARANCE_DEPLOY_PROBE   10 // Z Clearance for Deploy/Stow
#define Z_CLEARANCE_BETWEEN_PROBES  5 // Z Clearance between probe points
#define Z_CLEARANCE_MULTI_PROBE     5 // Z Clearance between multiple probes
#define Z_PROBE_LOW_POINT          -2 // Farthest distance below the trigger-point to go before stopping
#define Z_PROBE_OFFSET_RANGE_MIN -20
#define Z_PROBE_OFFSET_RANGE_MAX 20
#define X_ENABLE_ON 0
#define Y_ENABLE_ON 0
#define Z_ENABLE_ON 0
#define E_ENABLE_ON 0 // For all extruders
#define DISABLE_X false
#define DISABLE_Y false
#define DISABLE_Z false
#define DISABLE_E false             // Disable the extruder when not stepping
#define DISABLE_INACTIVE_EXTRUDER   // Keep only the active extruder enabled
#define INVERT_X_DIR false
#define INVERT_Y_DIR false
#define INVERT_Z_DIR false
#define INVERT_E0_DIR true
#define INVERT_E1_DIR false
#define INVERT_E2_DIR false
#define INVERT_E3_DIR false
#define INVERT_E4_DIR false
#define INVERT_E5_DIR false
#define INVERT_E6_DIR false
#define INVERT_E7_DIR false
#define X_HOME_DIR -1
#define Y_HOME_DIR -1
#define Z_HOME_DIR -1
#define X_BED_SIZE 300
#define Y_BED_SIZE 300
#define X_MIN_POS 0
#define Y_MIN_POS 0
#define Z_MIN_POS 0
#define X_MAX_POS X_BED_SIZE
#define Y_MAX_POS Y_BED_SIZE
#define Z_MAX_POS 400
#define MIN_SOFTWARE_ENDSTOPS
  #define MIN_SOFTWARE_ENDSTOP_X
  #define MIN_SOFTWARE_ENDSTOP_Y
  #define MIN_SOFTWARE_ENDSTOP_Z
  #define MIN_SOFTWARE_ENDSTOP_I
  #define MIN_SOFTWARE_ENDSTOP_J
  #define MIN_SOFTWARE_ENDSTOP_K
#define MAX_SOFTWARE_ENDSTOPS
  #define MAX_SOFTWARE_ENDSTOP_X
  #define MAX_SOFTWARE_ENDSTOP_Y
  #define MAX_SOFTWARE_ENDSTOP_Z
  #define MAX_SOFTWARE_ENDSTOP_I
  #define MAX_SOFTWARE_ENDSTOP_J
  #define MAX_SOFTWARE_ENDSTOP_K
#define AUTO_BED_LEVELING_BILINEAR
  #define ENABLE_LEVELING_FADE_HEIGHT
    #define DEFAULT_LEVELING_FADE_HEIGHT 10.0 // (mm) Default fade height.
  #define SEGMENT_LEVELED_MOVES
  #define LEVELED_SEGMENT_LENGTH 5.0 // (mm) Length of all segments (except the last one)
  #define GRID_MAX_POINTS_X 3
  #define GRID_MAX_POINTS_Y GRID_MAX_POINTS_X
#define Z_SAFE_HOMING
  #define Z_SAFE_HOMING_X_POINT X_CENTER  // X point for Z homing
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

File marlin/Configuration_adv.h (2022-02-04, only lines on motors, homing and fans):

#define E0_AUTO_FAN_PIN -1
#define E1_AUTO_FAN_PIN -1
#define E2_AUTO_FAN_PIN -1
#define E3_AUTO_FAN_PIN -1
#define E4_AUTO_FAN_PIN -1
#define E5_AUTO_FAN_PIN -1
#define E6_AUTO_FAN_PIN -1
#define E7_AUTO_FAN_PIN -1
#define CHAMBER_AUTO_FAN_PIN -1
#define COOLER_AUTO_FAN_PIN -1
#define COOLER_FAN_PIN -1
#define HOMING_BUMP_MM      { 5, 5, 2 }       // (mm) Backoff from endstops after first bump
#define HOMING_BUMP_DIVISOR { 2, 2, 4 }       // Re-Bump Speed Divisor (Divides the Homing Feedrate)
#define HOME_Y_BEFORE_X                     // If G28 contains XY home Y before X
#define MICROSTEP_MODES { 16, 16, 16, 16, 16, 16 } // [1,2,4,8,16]
    #define X_CURRENT       800        // (mA) RMS current. Multiply by 1.414 for peak current.
    #define X_CURRENT_HOME  500  // (mA) RMS current for sensorless homing
    #define X_MICROSTEPS     16        // 0..256
    #define Y_CURRENT       800
    #define Y_CURRENT_HOME  Y_CURRENT
    #define Y_MICROSTEPS     16
    #define Z_CURRENT       800
    #define Z_CURRENT_HOME  Z_CURRENT
    #define Z_MICROSTEPS     16
    #define E0_CURRENT      800
    #define E0_MICROSTEPS    16
  #define X_HYBRID_THRESHOLD     100  // [mm/s]
  #define X2_HYBRID_THRESHOLD    100
  #define Y_HYBRID_THRESHOLD     100
  #define Y2_HYBRID_THRESHOLD    100
  #define Z_HYBRID_THRESHOLD       3
  #define Z2_HYBRID_THRESHOLD      3
  #define Z3_HYBRID_THRESHOLD      3
  #define Z4_HYBRID_THRESHOLD      3
  #define I_HYBRID_THRESHOLD       3
  #define J_HYBRID_THRESHOLD       3
  #define K_HYBRID_THRESHOLD       3
  #define E0_HYBRID_THRESHOLD     30
  #define E1_HYBRID_THRESHOLD     30
  #define E2_HYBRID_THRESHOLD     30
  #define E3_HYBRID_THRESHOLD     30
  #define E4_HYBRID_THRESHOLD     30
  #define E5_HYBRID_THRESHOLD     30
  #define E6_HYBRID_THRESHOLD     30
  #define E7_HYBRID_THRESHOLD     30

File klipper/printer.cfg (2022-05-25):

[include mainsail.cfg]
# This file contains common pin mappings for the BIGTREETECH SKR V1.4
# board. To use this config, the firmware should be compiled for the
# LPC1768 or LPC1769(Turbo).

# See docs/Config_Reference.md for a description of parameters.

# Best run so far
# Velocity: 11000
# Accel: 18000
# SCV: 13
# Max A2D: 9300
# Speed 400%
# Max temp 250
#
# Notes:
#  Needs cooling fans
#  Need to fix initial print so it doesn't ooz in the print area
#  Need to make it so that the slicer is slower on longer sweeping corners, where the extruder just can't keep up

[mcu rpi]
serial: /tmp/klipper_host_mcu

[adxl345]
cs_pin: rpi:None

[resonance_tester]
accel_chip: adxl345
probe_points:
    150, 150, 20  # an example


[input_shaper]
shaper_freq_x: 79.2
shaper_type_x: mzv
shaper_freq_y: 86.6
shaper_type_y: ei


[stepper_x]
step_pin: P2.2
dir_pin: P2.6
enable_pin: !P2.1
microsteps: 16
rotation_distance: 32
endstop_pin: !P1.29
position_endstop: 0
position_max: 300
homing_speed: 50

[stepper_y]
step_pin: P0.19
dir_pin: !P0.20
enable_pin: !P2.8
microsteps: 16
rotation_distance: 32
endstop_pin: !P1.28
position_endstop: 0
position_max: 300
homing_speed: 50

[stepper_z]
step_pin: P0.22
dir_pin: P2.11
enable_pin: !P0.21
endstop_pin: probe:z_virtual_endstop
microsteps: 16
rotation_distance: 4
position_max: 400
position_min: -2

[extruder]
step_pin: P2.13
dir_pin: P0.11
enable_pin: !P2.12
microsteps: 16
rotation_distance: 4.637 # Orbiter 2.0
full_steps_per_rotation: 200 # Orbiter 2.0
#rotation_distance: 4.2057 # Sherpa Mini
nozzle_diameter: 0.400
filament_diameter: 1.750
heater_pin: P2.7
pressure_advance=0.082 # PLA / DRAGON HF
sensor_type: ATC Semitec 104GT-2
sensor_pin: P0.24
#control: pid
#pid_Kp: 22.2
#pid_Ki: 1.08
#pid_Kd: 114
min_temp: 0
max_temp: 260

#[extruder1]
#step_pin: P1.15
#dir_pin: P1.14
#enable_pin: !P1.16
#heater_pin: P2.4
#sensor_pin: P0.23
#...

[bltouch]
control_pin: P2.0 #ok
sensor_pin: P0.10 #ok
#pin_up_touch_mode_reports_triggered: True
x_offset: 46
y_offset: 8
#z_offset = 4

#[safe_z_home]
#home_xy_position: 150,150 # Change coordinates to the center of your print bed
#speed: 50
#z_hop: 10
#z_hop_speed: 5

[bed_mesh]
mesh_min: 50,50
mesh_max: 250,250
probe_count: 3,3
speed: 100
fade_end: 0.0
horizontal_move_z: 10

[heater_bed]
heater_pin: P2.5
sensor_type: NTC 100K MGB18-104F39050L32
sensor_pin: P0.25
#control: pid
#pid_Kp: 54.027
#pid_Ki: 0.770
#pid_Kd: 948.182
min_temp: 0
max_temp: 130

[fan]
pin: P2.3
max_power: 0.57

[mcu]
serial:  /dev/serial/by-id/usb-Klipper_lpc1769_21900005A49869AF23E03E5EC52000F5-if00

[printer]
kinematics: corexy
max_velocity: 8000
max_accel: 12000
max_z_velocity: 12
max_z_accel: 100

[homing_override]
set_position_z: 5
axes: xyz
gcode:
    G90
    G1 Z10 F600
    G90
    G28 Y 
    G28 X
    G1 X150 Y150 F5000
    G28 Z
    G1 Z5

[gcode_macro END_PRINT]
gcode:
    # Turn off bed, extruder, and fan
    M140 S0
    M104 S0
    M106 S0
    # Move nozzle away from print while retracting
    G91
    G1 X-2 Y-2 E-3 F300
    # Raise nozzle by 10mm  
    G1 Z10 F3000
    G90
    G1 X5 Y5 F5000
    # Disable steppers
    M84

[gcode_macro CANCEL_PRINT]
rename_existing: ORIG_CANCEL_PRINT
gcode:
  G91
  G1 Z10
  G90
  G1 X5 Y5 F5000
  ORIG_CANCEL_PRINT
 
 


########################################
# TMC2209 configuration
########################################

[tmc2209 stepper_x]
uart_pin: P1.10
run_current: 1.00

[tmc2209 stepper_y]
uart_pin: P1.9
run_current: 1.00
# .810 speed run

[tmc2209 stepper_z]
uart_pin: P1.8
run_current: 0.650

[tmc2209 extruder]
uart_pin: P1.4
# run_current: 0.400 # Sherpa Mini
run_current: 0.85
hold_current: 0.200 




########################################
# EXP1 / EXP2 (display) pins
########################################

[board_pins]
aliases:
    # EXP1 header
    EXP1_1=P1.30, EXP1_3=P1.18, EXP1_5=P1.20, EXP1_7=P1.22, EXP1_9=<GND>,
    EXP1_2=P0.28, EXP1_4=P1.19, EXP1_6=P1.21, EXP1_8=P1.23, EXP1_10=<5V>,
    # EXP2 header
    EXP2_1=P0.17, EXP2_3=P3.26, EXP2_5=P3.25, EXP2_7=P1.31, EXP2_9=<GND>,
    EXP2_2=P0.15, EXP2_4=P0.16, EXP2_6=P0.18, EXP2_8=<RST>, EXP2_10=<NC>
    # Pins EXP2_1, EXP2_6, EXP2_2 are also MISO, MOSI, SCK of bus "ssp0"

# See the sample-lcd.cfg file for definitions of common LCD displays.

#*# <---------------------- SAVE_CONFIG ---------------------->
#*# DO NOT EDIT THIS BLOCK OR BELOW. The contents are auto-generated.
#*#
#*# [extruder]
#*# control = pid
#*# pid_kp = 30.112
#*# pid_ki = 1.792
#*# pid_kd = 126.470
#*#
#*# [heater_bed]
#*# control = pid
#*# pid_kp = 63.062
#*# pid_ki = 1.518
#*# pid_kd = 655.056
#*#
#*# [bltouch]
#*# z_offset = 2.740
#*#
#*# [bed_mesh default]
#*# version = 1
#*# points =
#*# 	-0.152500, 0.021250, -0.043750
#*# 	-0.098750, 0.077500, -0.130000
#*# 	0.117500, 0.152500, -0.092500
#*# tension = 0.2
#*# min_x = 50.0
#*# algo = lagrange
#*# y_count = 3
#*# mesh_y_pps = 2
#*# min_y = 50.0
#*# x_count = 3
#*# max_y = 250.0
#*# mesh_x_pps = 2
#*# max_x = 250.0

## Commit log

2022-01-23 Added stl
    [ft5.stl]
2022-01-23 Started work on rear corner brackets
    [ft5.scad, ft5.stl]
2022-01-23 Updated belt path, added colors for extruder and rails
    [ft5.scad, ft5.stl]
2022-01-23 Moved pully definition
    [ft5.scad]
2022-01-24 Initial cut at mounts
    [ft5.scad, ft5.stl]
2022-02-04 major update after first working version
    [Configuration.h, Configuration_adv.h, MakerBot_Endstop.stl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]
2022-02-04 Added EVA compatible hemera mount
    [cable_holder.stl, front_belt_mount.stl, mount.stl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]
2022-02-04 Updated carriage mount
    [5015_Blower_Fan.stl, bl_touch_mount.stl, cable_holder.stl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]
2022-05-09 Updated with new x endstop mount, an d carbon fiber tube parts
    [ft5.scad, left_motor_mount.stl, left_xy_carriage_mount_lower_al_2020.stl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]
2022-05-09 Removed uneeded files and added missing changes
    [left_xy_carriage_mount_lower.stl, left_xy_carriage_mount_upper.stl, pulley_spacer.scad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]
2022-05-17 Updated for drill jig
    [ft5.scad, left_motor_mount.stl, left_xy_carriage_mount_lower_al_2020.stl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]
2022-05-25 Added bom
2022-05-25 Added printer config for klipper
    [printer.cfg]

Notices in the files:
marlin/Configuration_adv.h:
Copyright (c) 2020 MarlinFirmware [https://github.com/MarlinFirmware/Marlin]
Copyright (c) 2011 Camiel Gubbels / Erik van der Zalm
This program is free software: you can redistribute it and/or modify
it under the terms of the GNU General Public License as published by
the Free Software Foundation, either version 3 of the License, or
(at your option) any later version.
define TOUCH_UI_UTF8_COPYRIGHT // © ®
